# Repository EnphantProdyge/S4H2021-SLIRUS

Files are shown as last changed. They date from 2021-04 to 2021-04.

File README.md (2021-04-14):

# Project-SLIRUS
Articulated robotic hand designed for sign language interpretation
Continuation from the SLEARH project: https://github.com/UdeS-GRO/S4H2020-SLEARH

# Preriquisites:
Hardware:
  - Open CR;
  - 1 usb to micro usb;
  - 1 drive for the motors ( (PCA-96 85) link: https://www.sunfounder.com/pca9685-16-channel-12-bit-pwm-servo-driver.html);
  - 12 electrical step motors ((Smraza 9G Micro Servo Motor) link: https://www.amazon.ca/gp/product/B0886351PP/ref=ppx_yo_dt_b_asin_title_o00_s00?ie=UTF8&psc=1);
  - RaspberryPi 3B+;
  - Micro-SD card (for RPi image);
  - 2 Dynamixel XL-430;
  - A voltage source with a current limit of more than 2 A;
  - 12 V power source, to 5.1mm center positive barrel jack;
  - Piece of plywood 30cm by 30cm (optional, but recommended);
  
Software;
  - Python 3.7(installed for this gitProject, but not necessarily needed);
  - Python Library:
    - pySerial;
    - tkinter;
  - Arduino IDE for the compiler;
  - Arduino Library:
    - Adafruit_PWMServoDriver.h;
    - ArduinoJson.h;
    - Wire.h;
    (But they all should be downloaded with the plateformio.ini)
  -Qt (5.7.1 or newer)
    
# Steps to start your project:
  - Read the Mechanics/README.md for informations on how to build the hand;
  - Read the Electrics/README.md for informations on how to plug the motors and the drive on the arduino;
  - Read the Interface/README.md for informations on how to use the interface
  - Read the Speech_to_text/README.md for informations on how to install the necessary librairies for the speech-to-text and create a key for the API connection
  - Install your favorite python IDE;
  - Open this git repo in a new project and create a python RunTool for UI_Main_Script.py script (that's where the application starts);
  - Install pySerial on your computer (it will appears in your python <python path>/Lib/*);
  (Now, your python side of the project should be up to run)
  - Install VsCode on your computer;
  - Install plateformio and ArduinoIDE in your vscode;
  - Set your Arduino_debug.exe path in your VsCode setups;
  - Build the project one first time (and it should load all the needed libraries);
  (Now, your Arduino side of the project should be up to run)
  - Import OpenCr library as shown in this video: https://www.youtube.com/watch?v=dQw4w9WgXcQ
  - Plug the Arduino to your computer and start the UI_Main_Script.py to start the application and the Arduino thread!
  
 # Steps to be able to run to application on the Raspberry Pi 3b+
  - Flash your Micro-SD card with an up to date RPi image running a linux operating system (you can flash your Micro-SD card with this       tool: https://www.balena.io/etcher/);
  - Connect your Micro-SD card in your RPi and open it with an internet cable or via VMWare for example;
  - On the first RPi's run, set your preferences;
  - Now, open a terminal and instal python 3.6 (or niewer, this could take some time) (this link could be usefull: https://github.com/instabot-py/instabot.py/wiki/Installing-Python-3.7-on-Raspberry-Pi);
  - Install the PySerial library with:
    $ sudo apt-get install pyserial
  - If you're connected to your RPi via VMWare or ssh, run this command:
    - $ export DISPLAY=:0
  - Create your project directory where you want it on your RPi:
    - $ cd "DIRECTORY PATH"
    - $ mkdir "PROJECT NAME"
    - $ cd "PROJECT NAME"
    - $ git clone "THE PROJECT'S LINK"
    - $ git pull
  - The project should now be copied locally onto your RPi;
  
  - Now go to the project's Ui_Main_script.py path on your RPi and run the program through a terminal:
    - $ python Ui_Main_Script.py
  
# Now Have Fun !

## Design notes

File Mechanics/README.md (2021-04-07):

ASSEMBLY OF THE HAND

1. Start by opening the BOM file in this folder.
2. With a 3D printer at 40% fill and supports, print all the parts that have &quot;3D printed&quot; as a link. Some parts need to be printed more than once, refer to the quantity column of the BOM to know how many.
3. Cut all the pivot rods with lenghts and quantity as described in the BOM (index 15-16)
4. Separate all the printed parts for each of the fingers where each number is the index in the BOM;

Pinky: 2 – 6 – 4 – 5

Ring finger: 2 – 6 – 4 – 5

Middle finger: 1 – 6 – 4 – 5

Index finger: 1 – 6 – 4 – 5 - 13 - 10 - 18

Thumb: 3 – 6 – 8 – 10 – 9 - 12

The assembly of the fingers is done with rods that are used as pivots in the joints. The servos' moving lever are fixed on the 3D printed levers with nails. The nail's head holds the lever in place and the other end is press fitted into the 3d printed lever.

Assembly of the pinky finger:
1. Attach part 2 and 6 with a 14mm pin. The assembly should be able to move freely.
2. Attach part 2 and 4 together with a 14mm pin.
3. Screw a Servo on part 6.
4. Attach part 5 and 6 with a 14mm pin.
5. With a nail, attach part 4 to the servo screwed on part 6.
6. Screw a servo on part 7.
7. With a nail, attach part 5 to the servo screwed on part 7.

For the four other fingers follow the same steps as for the pinky finger using the parts specified earlier.

When the fingers are assembled, the servo holders are cliped on the palm and a rod is inserted in the pivot.

Assembly of the base:
8. Install the motors drive on the back of the hand with the four bolts of index 29.
9. Make all the electric connections relating to the hand motors as explained in the electric README.
10. Insert a rod of index 26 into the forearm (index 20) until the exposed part of the rod is roughly the same length as the thickness of the base.
11. With the bolts of index 28, install the Open CR and the raspberry pi on the forearm.
12. Insert one of the Dynamixel in the cage located on the forearm until the rotating circle is level with the exterior of the cage.
13. Fasten the 3D printed piece of index 23 to the Dynamixel installed in step 24 using 2 bolts of index 27.
14. Insert the other Dynamixel in the rectangular enclosure in the base, and fasten the gear of index 21 to said Dynamixel using 2 bolts of index 27.
15. Insert 2 bearings of index 22 in the circular grooves in the base.
16. Place the protruding rod of the forearm into the hols in the base, making sure that the gear installed in step 26 and the gear of the forearm mesh together.
17. Connect the hand to the forearm using a rod of index 25, making sure that the driver side of the palm faces the Dynamixel in the forearm.
18. Install the wrist lever arm (index 24) between the forearm dynamixel and the protruding hole at the bottom of the palm.
19. Connect the Dynamixels as explained in the electric README.
If desired, you can screw a wooden platform to the base for added stability.

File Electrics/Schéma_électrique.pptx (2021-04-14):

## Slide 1

PCA9685
16 CHANNEL 12-BIT PWM
I2C ADDRESS I[A5..A0][R/W]
VDD : 2.3-5.5V IO : 5V SAFE
OUTPUT : 25mA EACH/400mA TOTAL

GND PWM0
SDA PWM1
SCL PWM2
VCC PWM3
PWM4
PWM5
PWM6
PWM7
PWM8
PWM9
PWM10
PWM11
PWM12
PWM13
PWM14
PWM15

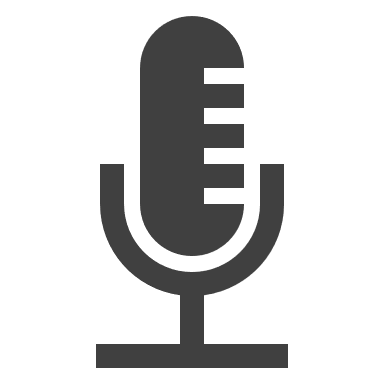
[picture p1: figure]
Micro de radio avec un remplissage uni

RASPBERRY PI

USB
USB
MICRO USB

OPENCR

GND
MICRO USB SDA
SCL
5V

POWER
SMPS IN

SERVO SG90-1
SERVO SG90-2
SERVO SG90-3
SERVO SG90-4
SERVO SG90-5
SERVO SG90-6
SERVO SG90-7
SERVO SG90-8
SERVO SG90-9
SERVO SG90-10
SERVO SG90-11
SERVO SG90-12

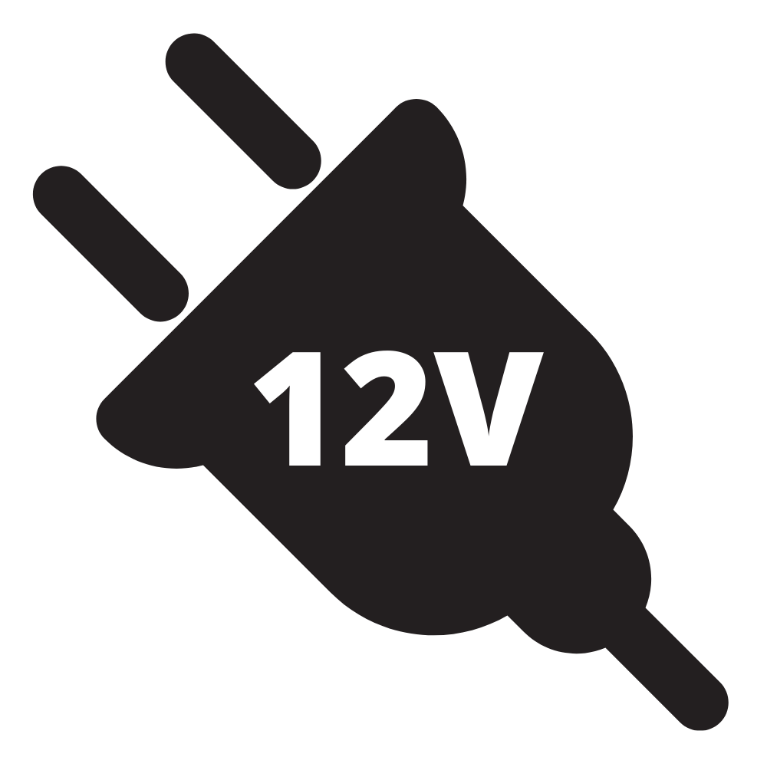
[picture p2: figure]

5V

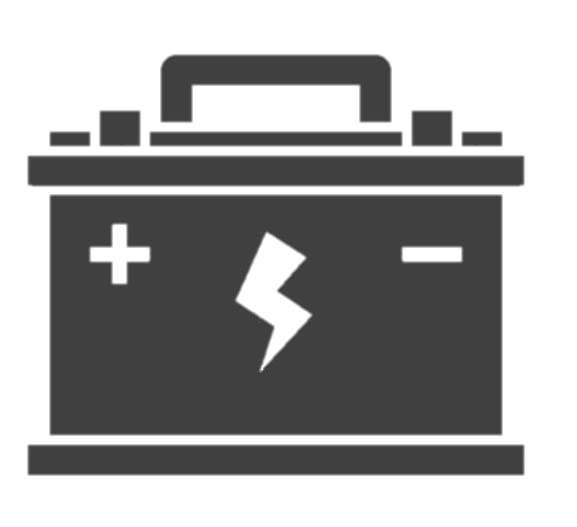
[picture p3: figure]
Car battery icon | Battery icon, Car battery, Car battery hacks

5V

AUXILIARY POWER
V+
GND

GND EXTCLK WHEN NOT IN USE

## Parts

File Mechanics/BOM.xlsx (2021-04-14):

Index | Part name | Qty | 3DPrinted | Description
1 | Phalange_Index-MiddleFinger | 2 | x | Index and middle finger end
2 | Phalange_RingFinger-PinkyFinger | 2 | x | Ring and Pinky finger end
3 | Phalange_thumb | 1 | x | Thumb finger end
4 | Finger_lever_distal | 4 | x | Lever for the four finger ends (except thumb)
5 | finger_lever_proximal | 4 | x | Finger lever that links fingers to the palm
6 | SG-90 Servo Socket | 5 | x | Servo Holder (part of the fingers)
7 | Servo Holder | 4 | x | Fix servo on the palm
8 | Thumb_Finger_lever_distal | 1 | x | Finger lever to move thumb end
9 | Proximal_thumb_lever | 1 | x | Lever to move thumb second part
10 | SG90 - Servo Socket_thumb | 1 | x | Servo socket (part ofthe thumb)
11 | Servo_holder_index | 1 | x | Holds servo on the index
12 | Thumb_lever | 1 | x | Lever for the whole thumb
13 | Palm_index | 1 | x | Part of the palm for index movement
14 | Palm | 1 | x | Palm
15 | 14mm pivot rod | 21 |  | 2mm x 14mm
16 | 17mm pivot rod | 2 |  | 2mm x 17mm
17 | SG90 micro servo | 12 |  | Servos to move the fingers
18 | palm_index_lever | 1 | x | Moves the index finger assembly
19 | Base | 1 | x | Allows rotation of the arm
20 | Arm | 1 | x | Forearm of the hand
21 | Gear | 1 | x | Rotates in order to rotate arm
22 | Flanged Ball Bearing | 2 |  | 1/4" ID x 1/2" OD
23 | Dynamixel_Coupler | 1 | x | Connects Dynamixel servo to lever arm
24 | Wrist_lever | 1 | x | Allows rotation of the wrist
25 | 1/4" x 4" D-shaft | 1 |  | Pivot for the wrist
26 | 1/4" x 8" D-shaft | 1 |  | Connects arm to base and allows rotation
27 | M2.0 bolt | 4 |  | Used to fix pieces to dynamixel
28 | M3-0.5 | 4 |  | Used to fasten open CR to Arm
29 | M2.5-0.45 | 4 |  | Used to fasten drive to hand

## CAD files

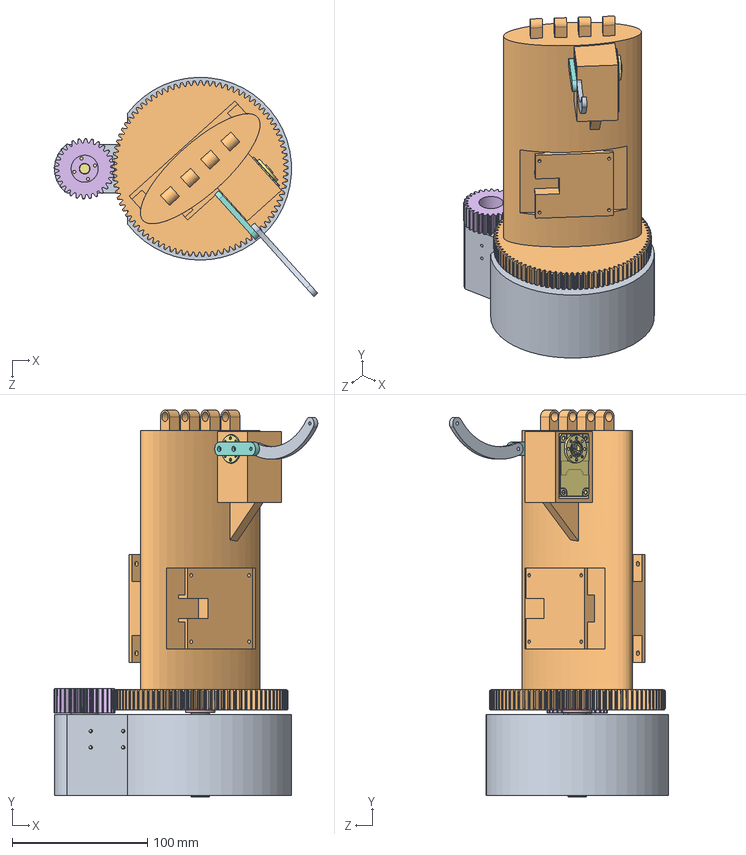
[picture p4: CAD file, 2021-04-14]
Mechanics/CAD/Arm_Base_Assembly.SLDASM
194.7 x 285.8 x 162.0 mm
Base
Arm
8632T144_D-PROFILE SHAFT
plain washer xlarge grade c_iso
Gear
XL-430 x 2
Dynamixel_Coupler
Wrist_lever

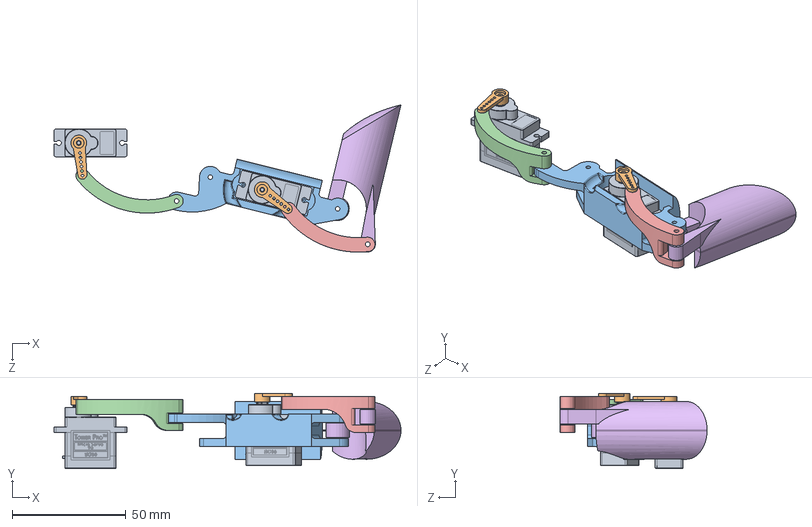
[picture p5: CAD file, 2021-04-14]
Mechanics/CAD/Ring_PinkyFinger.SLDASM
152.6 x 33.0 x 64.7 mm
SG90 - Micro Servo 9g - Tower Pro.1 x 2
SG90 - Micro Servo 9g - Tower Pro.2 x 2
SG90 - Servo Socket
finger_lever_proximal
Finger_lever_distal
phalange_RingFinger-PinkyFinger

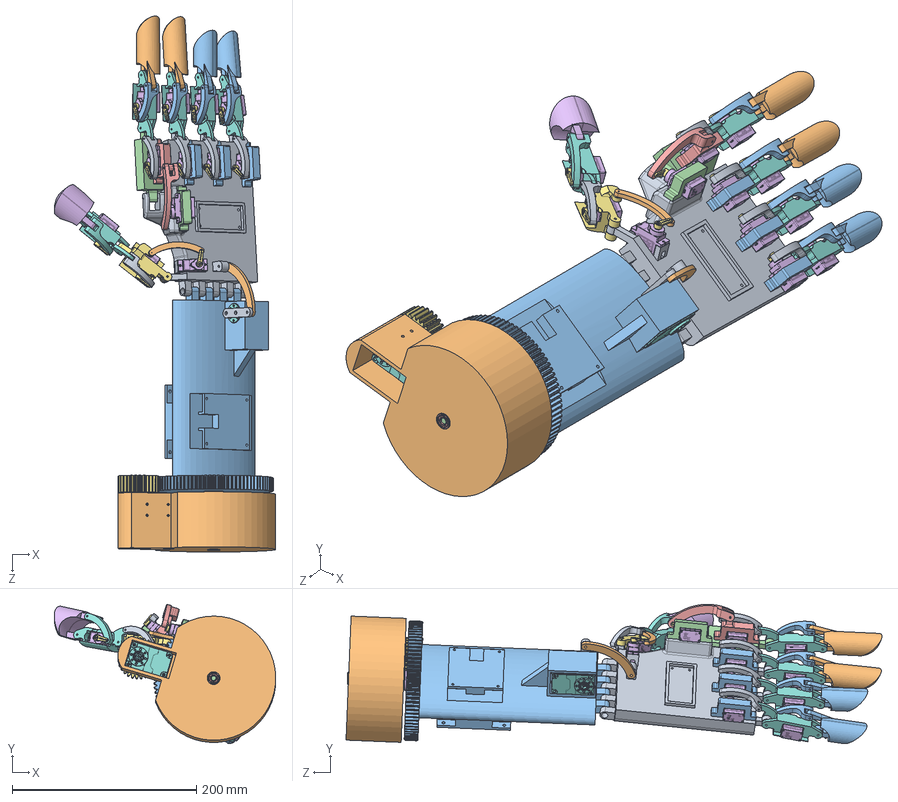
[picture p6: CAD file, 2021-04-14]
Mechanics/CAD/hand.SLDASM
240.7 x 151.5 x 582.4 mm
Palm
Base
Arm
8632T144_D-PROFILE SHAFT
plain washer xlarge grade c_iso
Gear
XL-430 x 2
Dynamixel_Coupler
Wrist_lever
ServoHolder x 3
Palm_index
Servo_Holder_index
SG90 - Micro Servo 9g - Tower Pro.1 x 12
SG90 - Micro Servo 9g - Tower Pro.2 x 12
SG90 - Servo Socket x 5
finger_lever_proximal x 4
phalange_Index-MiddleFinger x 2
Finger_lever_distal x 4
ServoHolder -palm_index
palm_index_lever
phalange_thumb
SG90 - Servo Socket_thumb
Thumb_finger_lever_distal
Proximal_thumb_lever
Thumb_lever
phalange_RingFinger-PinkyFinger x 2

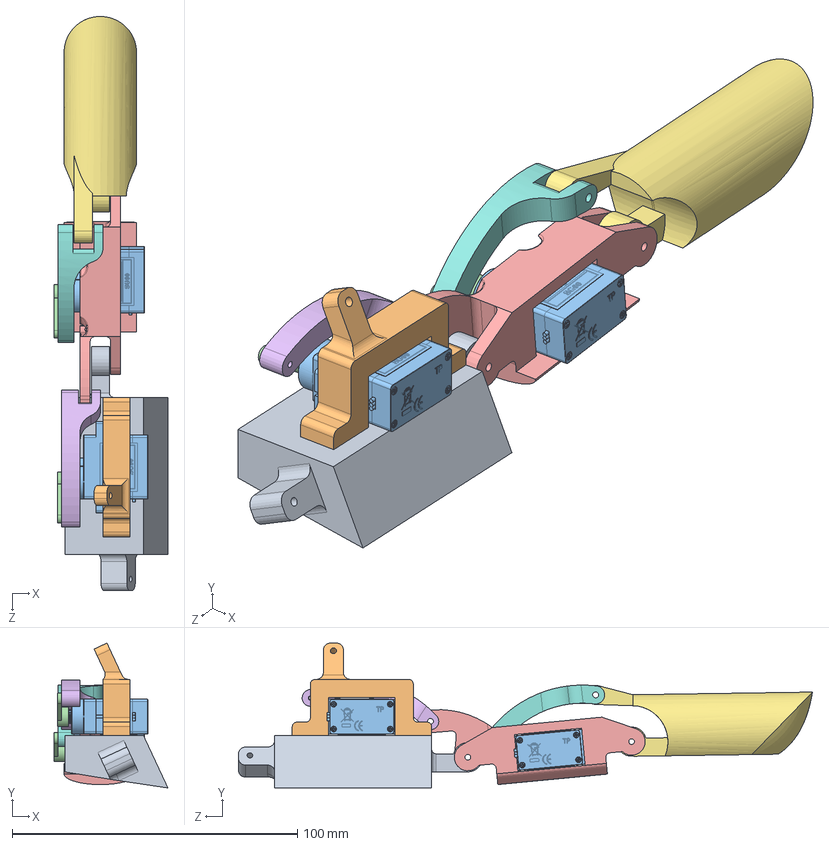
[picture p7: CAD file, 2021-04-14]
Mechanics/CAD/Index.SLDASM
39.9 x 50.8 x 201.2 mm
Palm_index
Servo_Holder_index
SG90 - Micro Servo 9g - Tower Pro.1 x 2
SG90 - Micro Servo 9g - Tower Pro.2 x 2
SG90 - Servo Socket
finger_lever_proximal
phalange_Index-MiddleFinger
Finger_lever_distal

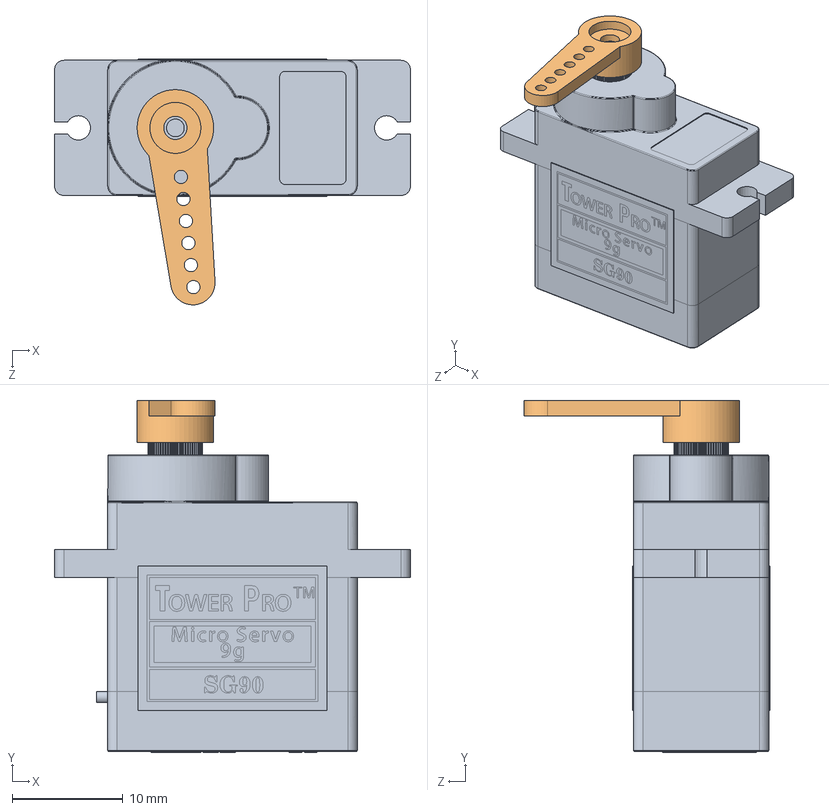
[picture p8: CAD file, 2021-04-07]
Mechanics/CAD/SG90 - Micro Servo Assembly.SLDASM
32.1 x 31.8 x 22.2 mm
SG90 - Micro Servo 9g - Tower Pro.1
SG90 - Micro Servo 9g - Tower Pro.2

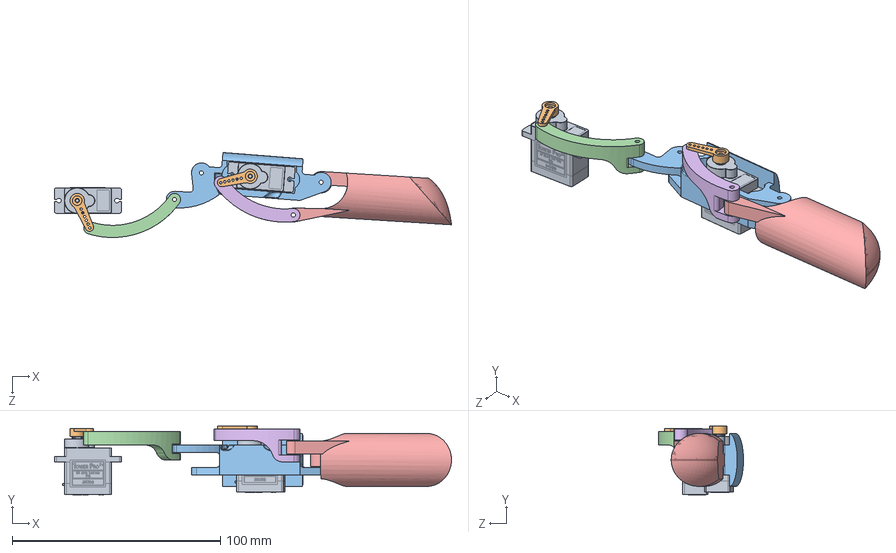
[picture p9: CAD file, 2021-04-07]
Mechanics/CAD/Index_MiddleFinger.SLDASM
190.4 x 33.0 x 40.8 mm
SG90 - Micro Servo 9g - Tower Pro.1 x 2
SG90 - Micro Servo 9g - Tower Pro.2 x 2
SG90 - Servo Socket
finger_lever_proximal
phalange_Index-MiddleFinger
Finger_lever_distal

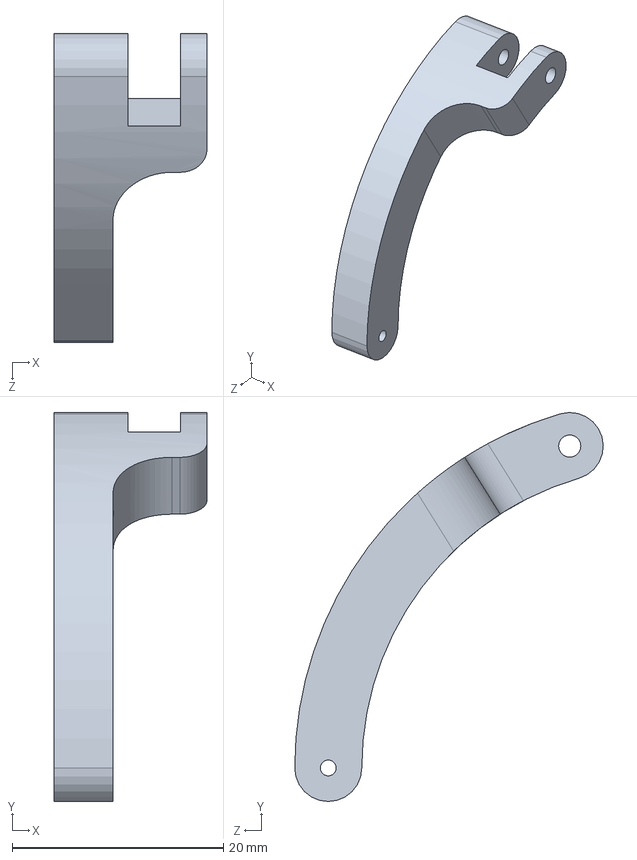
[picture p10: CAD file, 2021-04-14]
Mechanics/CAD/Proximal_thumb_lever.SLDPRT
14.5 x 36.8 x 29.2 mm

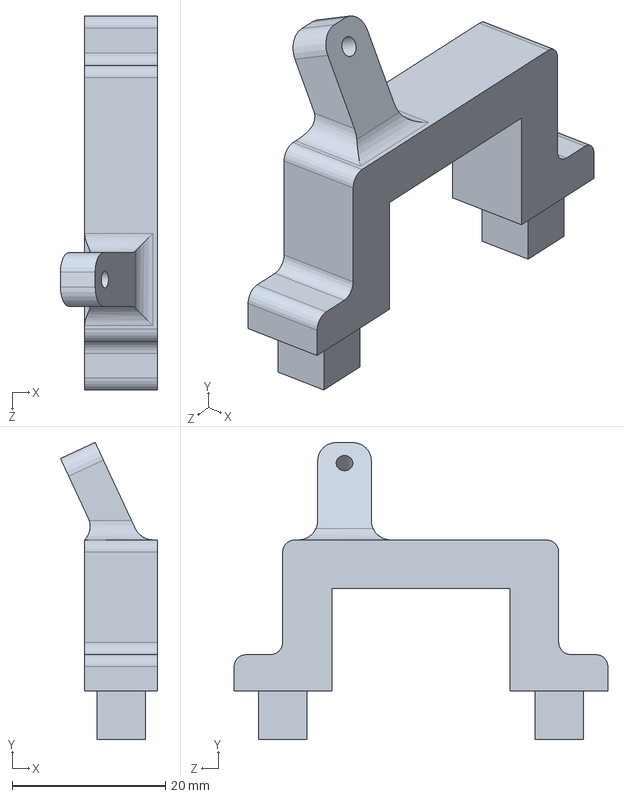
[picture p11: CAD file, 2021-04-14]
Mechanics/CAD/Servo_Holder_index.SLDPRT
12.7 x 38.8 x 48.9 mm

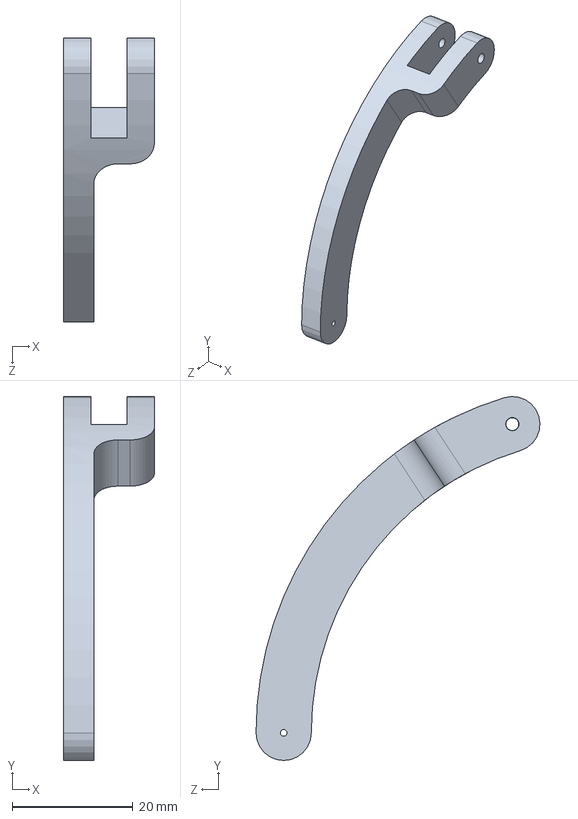
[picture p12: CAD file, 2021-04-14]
Mechanics/CAD/palm_index_lever.SLDPRT
15.0 x 60.2 x 46.9 mm

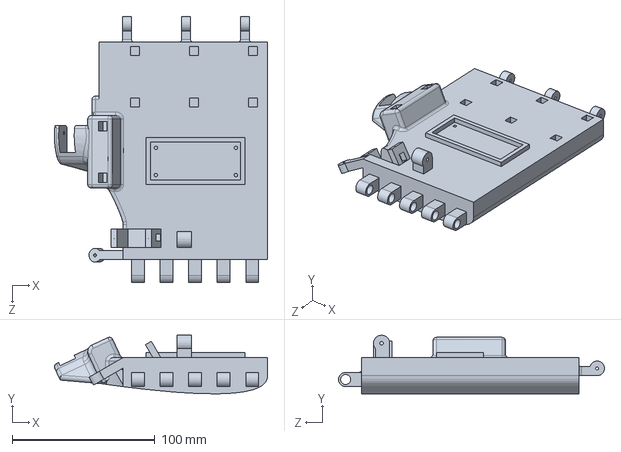
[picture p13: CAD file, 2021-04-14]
Mechanics/CAD/Palm.sldprt
149.3 x 41.1 x 186.2 mm

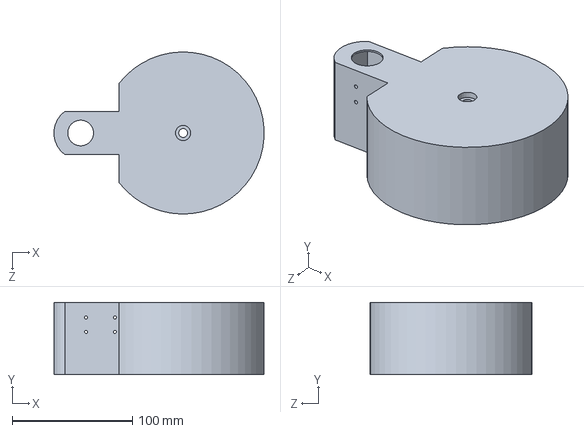
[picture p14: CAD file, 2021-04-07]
Mechanics/CAD/Base.SLDPRT
174.9 x 60.0 x 135.0 mm

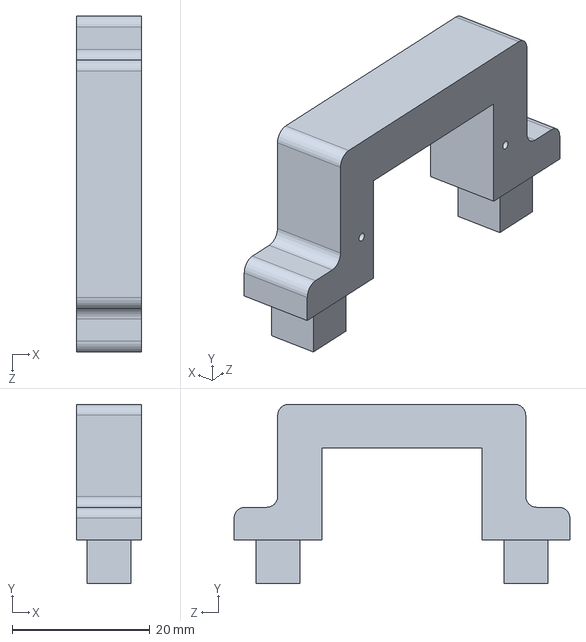
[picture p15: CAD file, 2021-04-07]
Mechanics/CAD/ServoHolder -palm_index.SLDPRT
9.53 x 26.1 x 48.9 mm

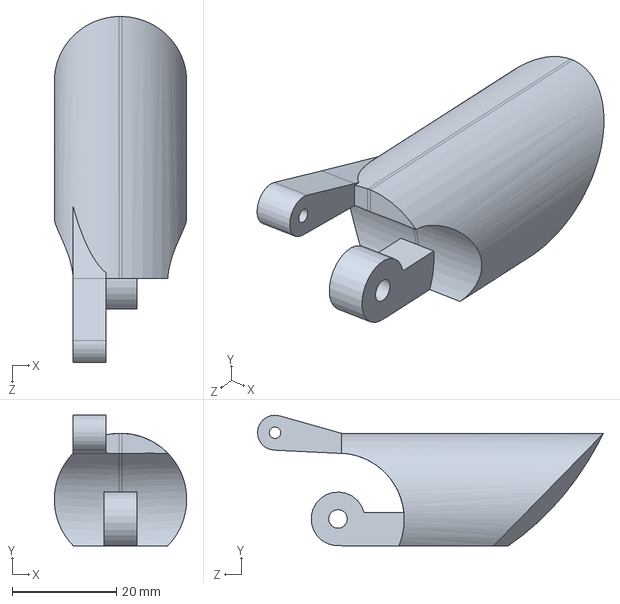
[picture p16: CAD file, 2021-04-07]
Mechanics/CAD/phalange_RingFinger-PinkyFinger.SLDPRT
25.4 x 25.1 x 66.4 mm

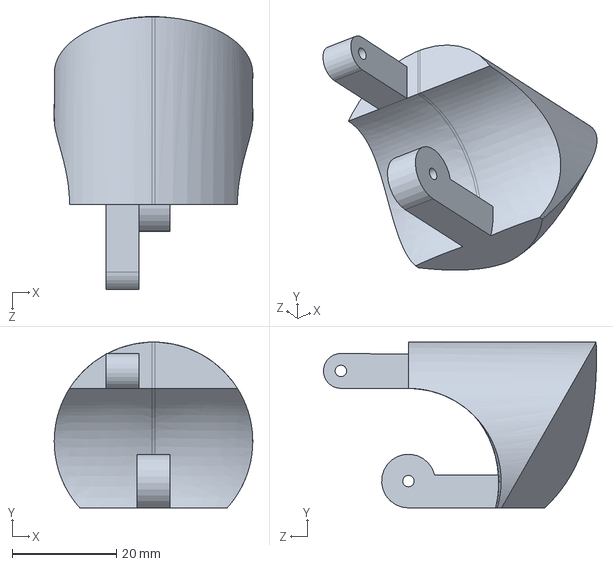
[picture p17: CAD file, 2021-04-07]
Mechanics/CAD/phalange_thumb.SLDPRT
38.1 x 31.8 x 52.4 mm

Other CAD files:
Mechanics/CAD/SG90 - Micro Servo 9g - Tower Pro.1.SLDPRT
Mechanics/CAD/Thumb_lever.SLDPRT
Mechanics/CAD/Finger_lever_distal.SLDPRT
Mechanics/CAD/SG90 - Servo Socket.SLDPRT
Mechanics/CAD/535198.SLDPRT
Mechanics/CAD/8632T144_D-PROFILE SHAFT.SLDPRT
Mechanics/CAD/Arm.SLDPRT
Mechanics/CAD/BD_petit.SLDPRT
Mechanics/CAD/Dynamixel_Coupler.SLDPRT
Mechanics/CAD/Gear.SLDPRT
Mechanics/CAD/Palm_index.sldprt
Mechanics/CAD/SG90 - Micro Servo 9g - Tower Pro.2.SLDPRT
Mechanics/CAD/SG90 - Servo Socket_Pouce2.SLDPRT
Mechanics/CAD/SG90 - Servo Socket_thumb.SLDPRT
Mechanics/CAD/Thumb_finger_lever_distal.SLDPRT
Mechanics/CAD/Wrist_lever.SLDPRT
Mechanics/CAD/XL-430.sldprt
Mechanics/CAD/finger_lever_proximal.SLDPRT
Mechanics/CAD/phalange_Index-Annulaire.SLDPRT
Mechanics/CAD/phalange_Index-MiddleFinger.SLDPRT

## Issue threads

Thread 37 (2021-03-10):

Asservissement : Enchaînement du code lors d'une reception de string

fannybeaumier, 2021-03-10:
- Séparer le string en plusieurs caractères
- Enchainer plusieurs lettres une à la suite de l'autre.
- Ajouter un retour à la position initiale dans le main.

Closed 2021-03-10.

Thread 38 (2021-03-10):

Asservissement : Enchaînement du code lors d'une reception de string

fannybeaumier, 2021-03-10:
- Séparer le string en plusieurs caractères
- Enchainer plusieurs lettres une à la suite de l'autre.
- Ajouter un retour à la position initiale dans le main.

Closed 2021-03-17.

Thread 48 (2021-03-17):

Refaire la base

fannybeaumier, 2021-03-17:
- Nouvelle boîte pour le dinamixel du poignet pour maintenir mieux le moteur en place (CAD)
- Sur la surface verticale, ajouter les troues pour fixer le OpenCR (CAD)
- Impression de la nouvelle base
- Assemblage de la nouvelle base

Closed 2021-03-17.

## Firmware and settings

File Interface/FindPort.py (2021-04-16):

import sys
import glob
import serial
import serial.tools.list_ports
import json
import time

def serial_ports():

    if sys.platform.startswith('win'):
        ports = list(serial.tools.list_ports.comports())


    elif sys.platform.startswith('linux'):
        ports = list(serial.tools.list_ports.comports())
    else:
        raise EnvironmentError('Unsupported platform')

    result = []
    for port in ports:
        j = 0
        list2 = []
        for i in port:
            list2.insert(j,i)

            j+=1
        if sys.platform.startswith('win'):
            if "Arduino" in port[1] or "USB" in port[1]:
                result.append(port[0])
        elif sys.platform.startswith('linux') or sys.platform.startswith('cygwin'):
            #print(port[1])
            if "ACM0" in port[1] or "AMA0" in port[1]:
                result.append(port[0])
        else:
            raise EnvironmentError('Unsupported platform')
    return result


def SendStrToOpenCR(port,msg):
    
    ser = serial.Serial("/dev/ttyACM0", 57600, timeout=1)
    #ser = serial.Serial(port, 57600, timeout=1)
    ser.flush()
    line = ""

    ser.write(msg.encode('utf-8'))
    while line != "IM DONE" :
        #print(ser)
        line = ser.readline().decode('utf-8').rstrip()
        #print("patate")
        print(line)
        sys.stdout.flush()
        time.sleep(1)



if __name__ == '__main__':
    list = serial_ports()
    Str_port = list[0]
    #print(Str_port)
    string = input("Quel est le string?:\t")
    

    SendStrToOpenCR(Str_port,string)

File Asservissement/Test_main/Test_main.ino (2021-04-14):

/** @file Test_main.ino
 * @brief This file is the main program of the motors control.
 * 
 * This file contains the main loop of the project.
 * @author BEAUMIER, FANNY
 * @date 13/04/2021
 */
#include <Wire.h>
#include <Arduino.h>
#include <Adafruit_PWMServoDriver.h>
#include "controlServo.h"
#include <DynamixelWorkbench.h>
#include <string>
#include "Communication.h"
/**
 * @headerfile Wire.h "Wire.h"
 * @headerfile Arduino.h "Arduino.h"
 * @headerfile Adafruit_PWMServoDriver.h "Adafruit_PWMServoDriver.h"
 * @headerfile controlServo.h "controlServo.h"
 * @headerfile DynamixelWorkbench.h "DynamixelWorkbench.h"
 * @headerfile string.h "string.h"
 * @headerfile Communication.h "Communication.h"
 */

/** Communication variables:
 */
#define FREQUENCY   50                      ///< Frequency for the servo
#define BAUDRATE  57600                     ///< Baud rate for Arduino mega 2560
#define NB_FINGERS  5                       ///< Number of finger on the hand
#if defined(__OPENCM904__)
#define DEVICE_NAME "3"                     ///< Dynamixel on Serial3(USART3)  <-OpenCM 485EXP
#elif defined(__OPENCR__)
#define DEVICE_NAME ""
#endif 
COM_Arduino ROB; 

/** command variables
 */
String msg = "";
uint16_t model_number = 0;
uint16_t model_number2 = 0;
char result, result2;
int32_t position = 0;

/** Initiating the Servo class object.
 */
Servo servo;

void setup() {
  Serial.begin(BAUDRATE); 

  /** Initializing Dynamixel
   */
  dxl_wb.init(DEVICE_NAME, BAUDRATE); //Initialisation du systeme qui gere les moteurs
  result = dxl_wb.ping(11, &model_number);
  result2 = dxl_wb.ping(12, &model_number2);
  dxl_wb.setExtendedPositionControlMode(12);
  dxl_wb.setPositionControlMode(11);
  result = dxl_wb.setVelocityBasedProfile(11);
  result = dxl_wb.itemWrite(11,"Profile_Velocity",80 );
  result = dxl_wb.itemWrite(11,"Profile_Acceleration",20);
  result = dxl_wb.itemWrite(11,"Drive_Mode",0);
  dxl_wb.torqueOn(11);
  dxl_wb.torqueOn(12);

  /** Initializing Servo
   */
  pwm.begin();
  pwm.setPWMFreq(FREQUENCY);
  
  /** Initializing base
   */
  dxl_wb.itemRead(12,"Present_Position",&position);
  servo.setupBase(position);                ///< Set the base in the initial position (face front)

  /** Initializing fingers and wrist
   */
  for(int increment = 0; increment<NB_FINGERS; increment++){
      servo.servoOut('5',increment);        ///< Set the hand in the initial position
  }
}

void loop() {
  /** Change string to individual caracteres
   */
  if (ROB.Get_state() == 1){                ///< Waiting for input
    if(Serial.available()>0){               ///< Waiting for the serial port to receive an input 
        msg = ROB.ReadMessage();            ///< Reading the string sent
        ROB.Get_status();                   ///< Sending the status
        ROB.SendMessage(msg);               ///< Sending the message received
    }
  }
  if (ROB.Get_state() == 2){                ///< The hand is executing a message
    delay(500);
    char caracteres[sizeof(msg)+1];         ///< Creation of a char array that will containt all the letters of the message
    strcpy(caracteres, msg.c_str());        ///< Transfering the message to a string then in different letter in the char array
    for (int i = 0; i < (msg.length()); i++){
      delay(2000);                          ///< Delay between each letter, in initial position
      Serial.print("Interface:start:");     ///< Message to interface : start letter
      Serial.println(caracteres[i]);
      for(int increment = 0; increment<NB_FINGERS; increment++){
        servo.servoOut(caracteres[i],increment); ///< Set the hand in the letter position
      }
      delay(2000);                          ///< Time of the letter in position
        for(int decrement = NB_FINGERS-1; decrement >= 0; decrement--){
          servo.reverseMove(caracteres[i],decrement); ///< Replace the hand in the initial position
        }
      Serial.print("Interface:done:");      ///< Message to interface : finish letter
      Serial.println(caracteres[i]);
    }
   ROB.Set_state(3);                        ///< All the letter of the string/message are done
    
  }
  if (ROB.Get_state() == 3){                ///< All the letter of the string/message are done
    delay(500);
    Serial.println("Interface:exit");       ///< Message to interface : exit demonstration
    ROB.SendMessage("IM DONE");
    msg = "";                               ///< Setting the message to empty
    ROB.Set_state(1);                       ///< The hand is ready to receive another message
    
  }    
  
}

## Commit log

2021-01-21 Lecture du fichier audio dans le google cloud storage et ajout de la cle Lecture du fichier audio dans le google cloud storage et ajout de la cle
2021-01-27 Created common finger file, enlarged certain holes
    [Bras de levier-Bas.SLDPRT, Bras de levier-Haut.SLDPRT, Bras de levier.SLDPRT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]
2021-02-03 Fait le CAD de l'avant bras
    [Bras de levier-Haut.SLDPRT, Bras2.SLDPRT, Bras_Levier-Poignet.SLDPRT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]
2021-02-17 Aded rotating base files
    [535198.SLDPRT, 8632T144_D-PROFILE SHAFT.SLDPRT, Assemblage_Base.SLDASM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]
2021-02-24 Update mechanic pour release
    [535198.SLDPRT, 8632T144_D-PROFILE SHAFT.SLDPRT, Assemblage_Base.SLDASM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]
2021-03-17 Ajout des images individuelles et thread programme mais toujours a modifier
2021-03-17 Amelioration du programme pour la communication au OpenCR
2021-03-17 Amelioration des threads dans linterface
2021-03-24 Supression de documents double et de l'ancienne equipe
2021-03-29 Fonctionnement du bouton pour demarrer la traduction avec la main. Ajout d'une nouvelle fonctionnalite, traduire seulement un ou quelques caracteres a la fois
2021-03-30 Ajout du timer pour montrer les images en meme temps que la main
2021-04-03 Final update of mech pieces
    [535198.SLDPRT, 8632T144_D-PROFILE SHAFT.SLDPRT, 90001A403_TYPE 18-8 STAINLESS STEEL HEX NUT.SLDPRT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]
2021-04-03 Bom Modification
    [BOM.xlsx]
2021-04-03 BOM modif
    [BOM.xlsx]
2021-04-07 permet de modifier .idea/.name
2021-04-07 Creation du readme de linterface
2021-04-07 Changement de API connection a Speech_to_text
2021-04-14 BOM update
    [Arm_Base_Assembly.SLDASM, BOM.xlsx, Index.SLDASM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]
2021-04-16 interface montre limage en meme temps que la main robotisee grace a la communication FindPort
